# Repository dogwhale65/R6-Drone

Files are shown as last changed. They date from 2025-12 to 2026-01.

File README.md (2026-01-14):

# R6 Surveillance Drone

An open-source recreation of the surveillance drone from Rainbow Six Siege.




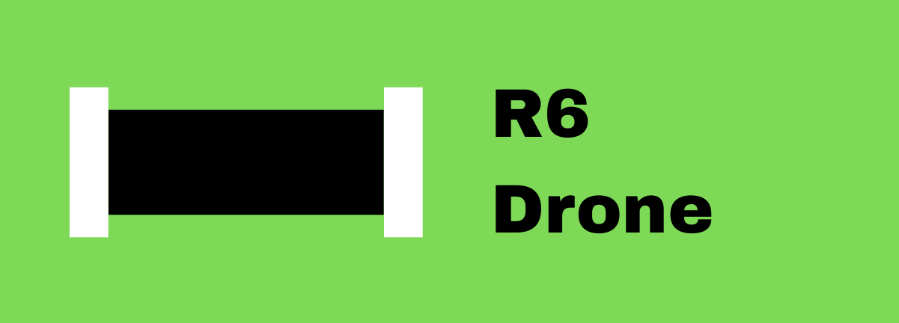
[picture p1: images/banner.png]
R6 Drone Banner


## About

I'm building a functional, 3D-printable version of the drone from R6 Siege. It features motorized wheels, LEDs, and a camera for FPV control.

Still early days — I've got the motors picked out and a rough CAD design, but there's plenty left to figure out.

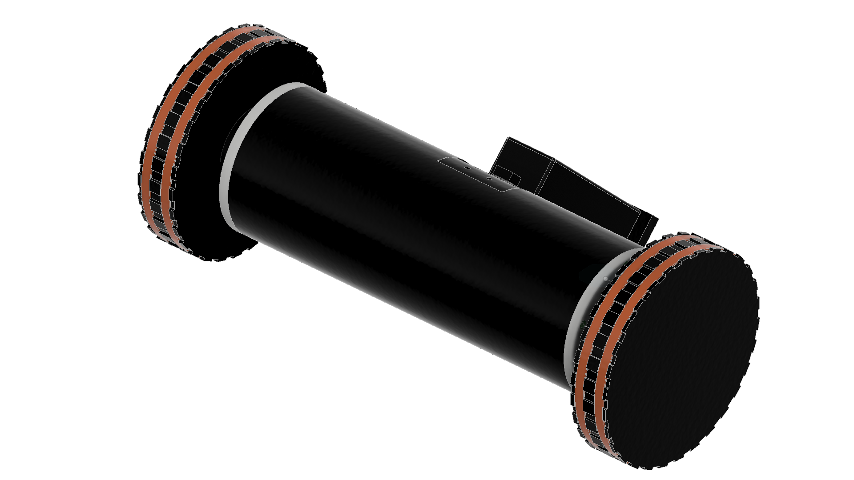
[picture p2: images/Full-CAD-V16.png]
Full CAD Design


The drone was designed to fit on a BambuLab P1S, so it may not be perfectly accurate to the in-game model. If anyone has the correct dimensions and wants to share them, I'm all ears!

I'm also *not* an engineer, so apologies if things don't work out perfectly. This is my first real project, and I'm learning as I go.

## Future Plans

- Dedicated controller
- Camera integration
- Battery level indicator

## Parts List

### Electronics

| Component | Model | Link | Qty |
| --- | ----- | ---- | --- |
| Battery | 11.1V 3S LiPo 2200mAh | [Amazon](https://www.amazon.com/dp/B07MQT6YJN) | 1 |
| Motors | 12V 550RPM | [Amazon](https://www.amazon.com/dp/B072R5G5GR) | 2 |
| Motor Driver | L298N H-Bridge | [Amazon](https://www.amazon.com/WWZMDiB-L298N-H-Bridge-Controller-Raspberry/dp/B0CR6BX5QL) | 1 |
| MCU | ESP32-S3 Dev Board | [Amazon](https://www.amazon.com/dp/B0C9GLDCRC?th=1) | 1 |
| Buck Converter | LM2596 DC-DC | [Amazon](https://www.amazon.com/dp/B08NV3JCBC) | 1 |
| XT60 Connectors | Male/Female pairs | [Amazon](https://www.amazon.com/dp/B0DB1LBGSH) | 1 pack |
| Power Switch | Rocker switch 10A, 20mm | [Amazon](https://www.amazon.com/dp/B07QQ22DTB) | 1 |
| Blue LEDs | 3mm diffused, 12V pre-wired | [Amazon](https://www.amazon.com/dp/B07T8FN8CS) | 1 pack |
| Wire | 18AWG silicone, multi-color | [Amazon](https://www.amazon.com/dp/B08BR454BX?th=1) | 1 pack |
| Heat Shrink | Assorted tubing kit | [Amazon](https://www.amazon.com/dp/B084GDLSCK) | 1 pack |
| LiPo Charger | 3S Charger | [Amazon](https://www.amazon.com/dp/B0B5GRRY59) | 1 |
| Camera | Generic Camera Module | [Amazon](https://www.amazon.com/dp/B012UXNDOY) | 1 |
| Wire Connectors | Lever nuts | [Amazon](https://www.amazon.com/dp/B0CJ5QF3VX) | 1 pack |

> **Heads up:** The motors I picked have a design flaw. Some mount holes go straight into the gearbox, so screws can hit the internals and prevent the motor from spinning. 

### 3D Printed Parts

Individual 3MF files are in `/3mf`. There's also a ready-to-print 3MF in the root folder with all parts pre-positioned and print settings configured.

> **Note:** These parts haven't been fully tested yet. They work for the most part, updates will be made as I test/improve them.

| Part | Qty | Notes |
| ---- | --- | ----- |
| Main Body | 1 | PLA or PETG, 20% infill, 3 walls, supports recommended |
| Battery Sled | 1 | PLA or PETG, 50% infill, 10 walls, support recommended |
| Motor Plates | 2 | PLA or PETG 20% infill, 5 walls |
| Wheels | 2 | TPU or PETG, 20% infill, 2 walls |

> It takes about 9 hours to print the main body and uses almost 400g of filament. I'm trying to incorporate as many features as possible into a single print to minimize this.

>The wheels are still being tested. TPU and PETG slip a lot. I'm currently working on a new design for the wheels, but cant print them at the current moment. I found out that if you just put some rubber bands around the wheels, it works just fine, but they fall off if you take a turn too hard. New wheel design will be posted soon, which has grooves for the rubber bands to stay in place better.

### Wheel Design Iterations

1. Just a simple cutout for the shaft. It stripped the wheels and obviously fell off.
2. Same principle but I added a screw hole to screw in and clamp onto the D-shaft. Worked good at preventing stripping, but still fell off.
3. A clamp system that used 2 screws to clamp around the shaft. Worked just about the same as the original wheel. The screws stripped the plastic before any real torque could be applied to it to actually clamp.
4. Current design, a separate hub that screws both onto/into the D-shaft and the wheel respectively. Haven't printed it yet, but I think it will work.

Print at 0.2mm layer height with supports where needed.

## Wiring

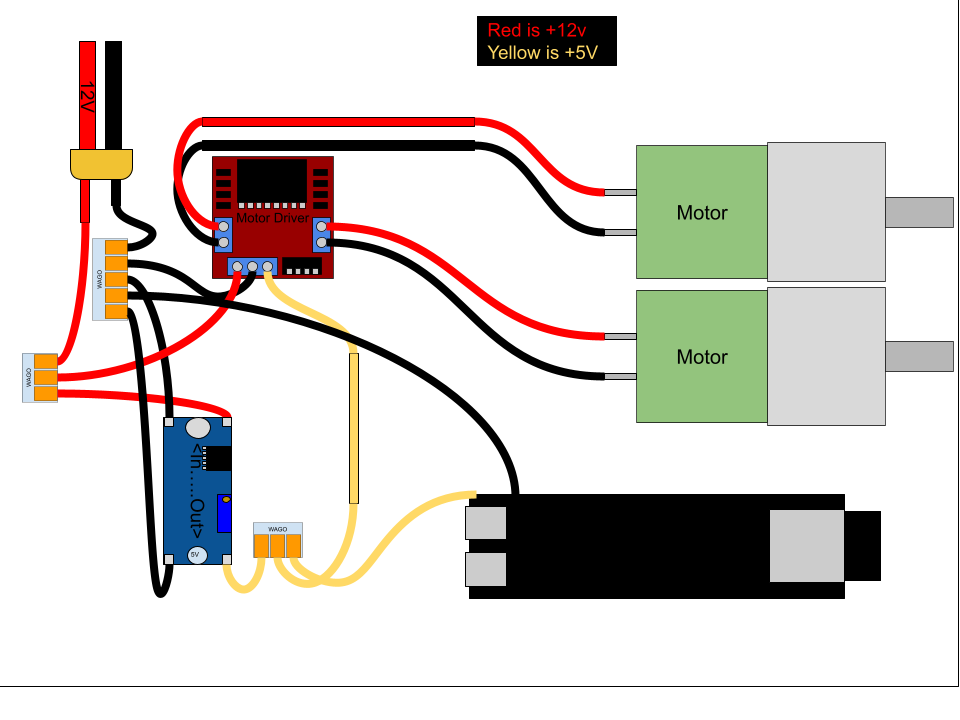
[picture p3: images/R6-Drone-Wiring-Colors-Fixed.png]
Wiring Diagram


**Notes:**

- This diagram doesn't include switches or extras.
- Logic wires aren't shown yet — I'll add them in a future revision.
- In my first build, I messed up my ESP32 and broke the 5V connection on my ESP32. I worked around it by adding a second buck converter and powering via the 3.3V pin instead.

Logic wires:

- ENA → GPIO 5
- IN1 → GPIO 6
- IN2 → GPIO 7
- ENB → GPIO 8
- IN3 → GPIO 9
- IN4 → GPIO 10

## Assembly

> **Note:** I used M3 x 20mm screws because I had them lying around. Shorter screws work for the motor plates, but I'd recommend at least 20mm for the main body.

1. Attach the motor plates to the motors, ensuring the motors can still spin freely.
2. Mount the motor plates to the bottom half of the main body.
3. Install the electronics inside the main body.
4. Attach the top half of the main body to the motor plates.
5. Secure the two body halves together.

## Code

The code is in `/code`. It runs a simple web server for controlling the drone. Connect to the drone's WiFi, open the web interface, and drive using on-screen joystick controls or WASD keys on a keyboard. Connect to it by connecting to the drone's WiFi network and visiting `http://192.168.4.1` in your browser. The default password is `password123` on the network `Robot-ESP32`

I am working on making an actual controller for it, rather than using my phone or a computer. Currently, there's a Bluetooth version for mobile app control.

## License

MIT — see [LICENSE](LICENSE).

---

[github.com/dogwhale65/r6-drone](https://github.com/dogwhale65/r6-drone)

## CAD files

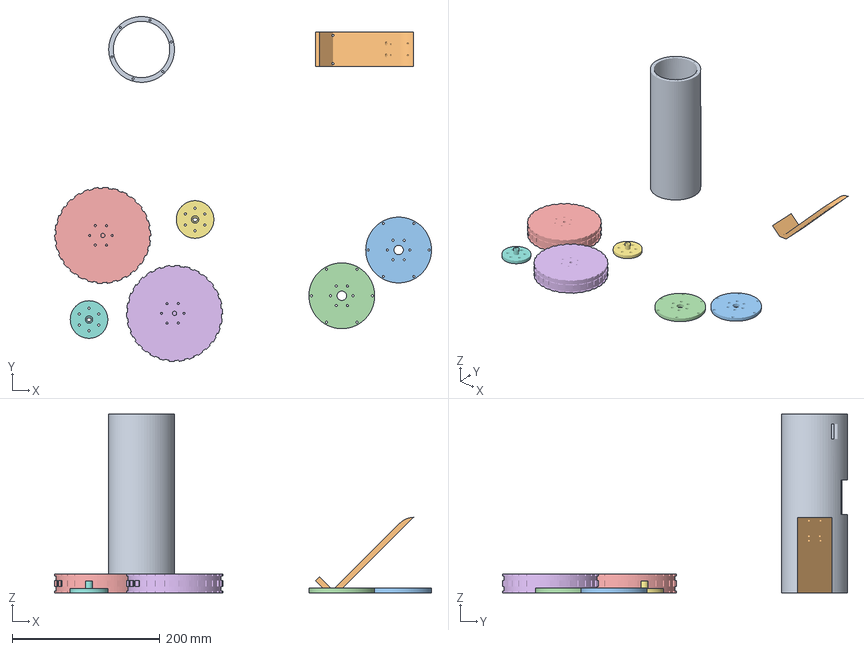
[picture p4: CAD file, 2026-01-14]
3mf/Full-Drone-BS.3mf
509.6 x 466.1 x 241.3 mm
Sled
Motor Plate x 2
Wheel (1) x 2

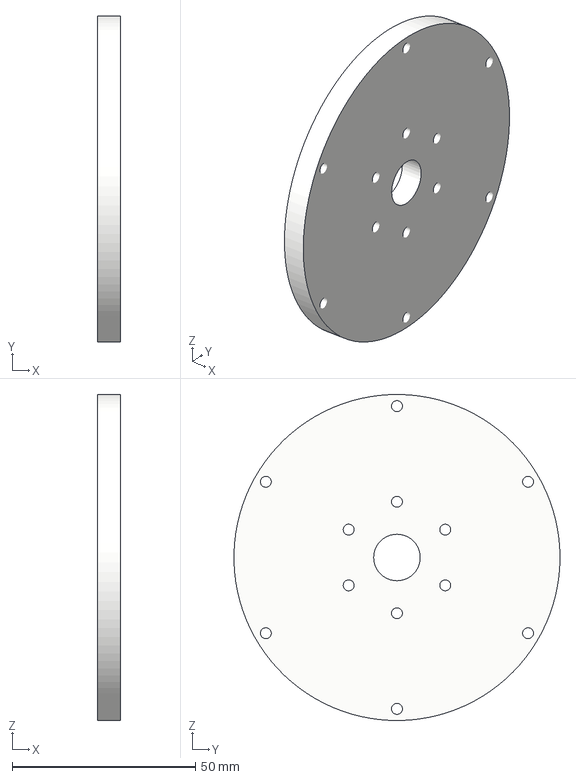
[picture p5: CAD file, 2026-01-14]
3mf/Motor-Plate.3mf
6.35 x 88.9 x 88.9 mm

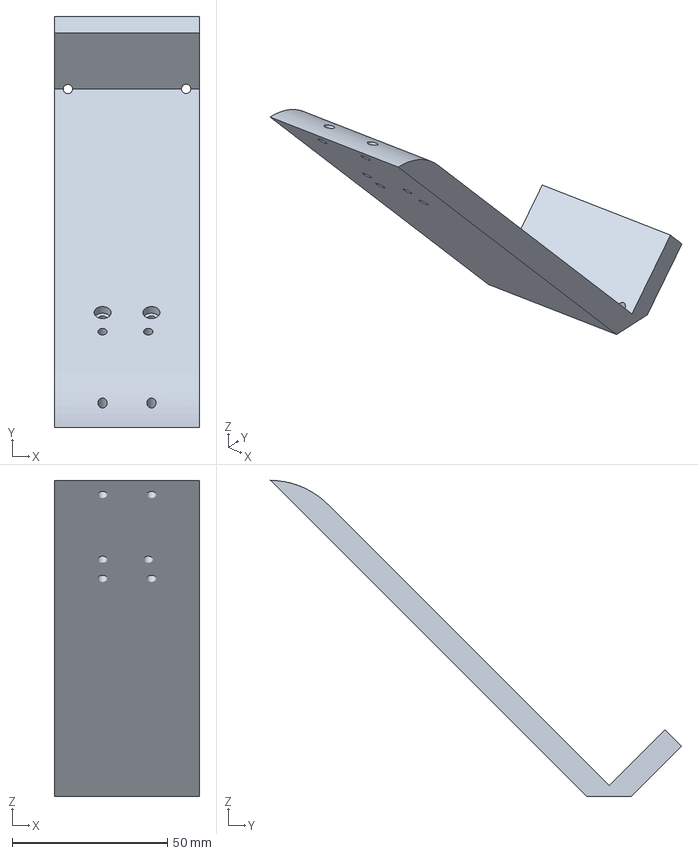
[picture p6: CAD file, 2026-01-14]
3mf/Battery-Sled.3mf
46.7 x 132.5 x 102.0 mm

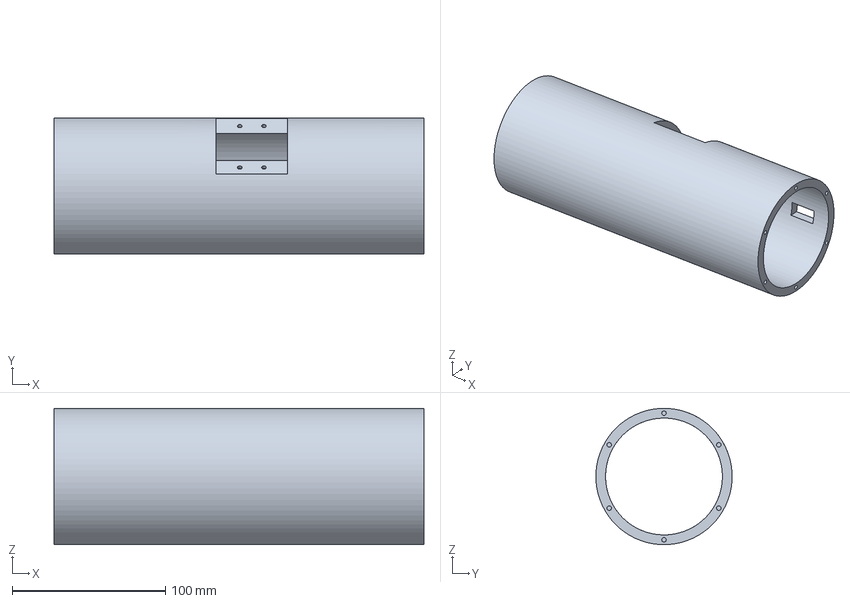
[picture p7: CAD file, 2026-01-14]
3mf/Body.3mf
241.3 x 88.9 x 88.9 mm

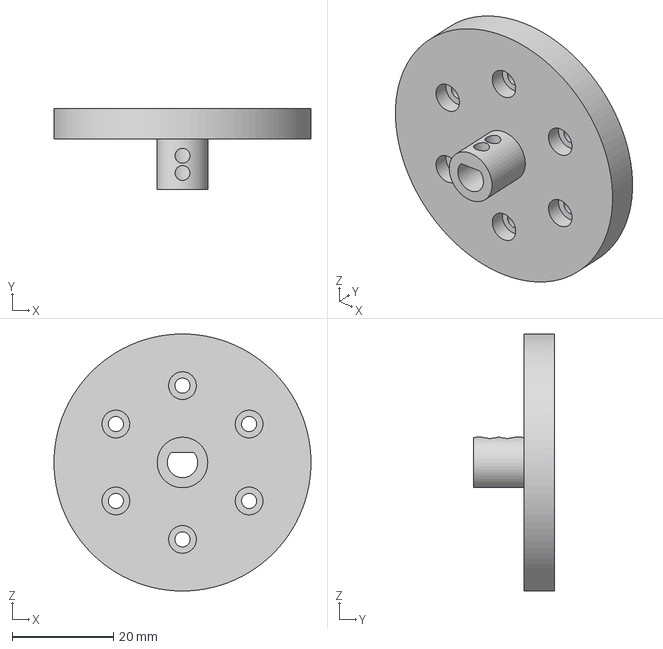
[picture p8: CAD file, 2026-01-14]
3mf/Wheel-Hub.3mf
50.8 x 16.0 x 50.8 mm

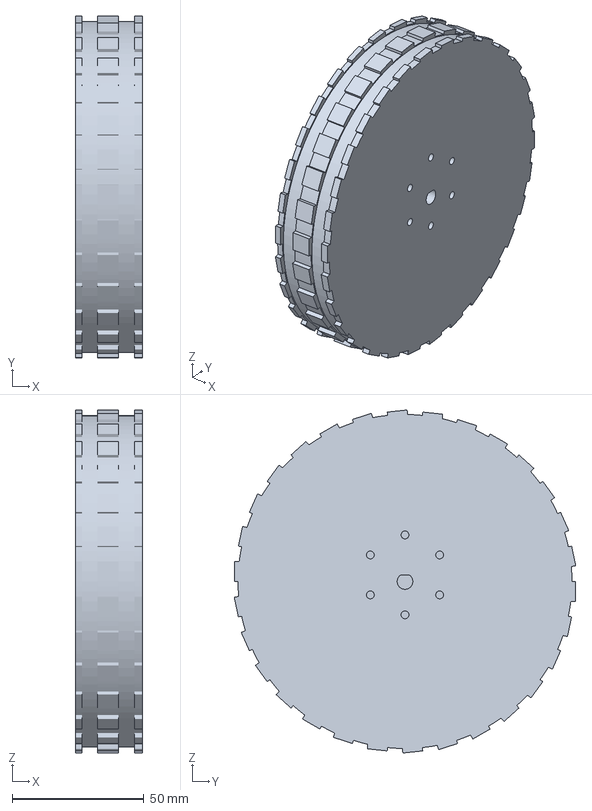
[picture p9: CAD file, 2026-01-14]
3mf/Wheel.3mf
25.4 x 129.9 x 130.4 mm

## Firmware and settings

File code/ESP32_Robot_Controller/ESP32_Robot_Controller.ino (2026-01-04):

#include <WiFi.h>
#include <WebServer.h>
#include <Adafruit_NeoPixel.h>

const char* ssid = "Robot-ESP32";
const char* password = "password123";

const int ENA = 5;
const int IN1 = 6;
const int IN2 = 7;
const int ENB = 8;
const int IN3 = 9;
const int IN4 = 10;

#define RGB_PIN 48
#define NUM_PIXELS 1
Adafruit_NeoPixel pixels(NUM_PIXELS, RGB_PIN, NEO_GRB + NEO_KHZ800);

const int pwmFreq = 20000;
const int pwmResolution = 8;

WebServer server(80);

int throttle = 0;
int rotation = 0;

void setLED(int r, int g, int b) {
  pixels.setPixelColor(0, pixels.Color(r, g, b));
  pixels.show();
}

void updateLED() {
  int r = 0, g = 0, b = 0;
  
  if (throttle > 10) { 
    r = 255; g = 255; b = 255; 
  } else if (throttle < -10) { 
    r = 255; g = 0; b = 0; 
  }
  
  if (rotation < -10) {
    if (throttle > 10) { 
      r = 0; g = 255; b = 255;
    } else if (throttle < -10) { 
      r = 255; g = 255; b = 0;
    } else { 
      r = 0; g = 255; b = 0;
    }
  } else if (rotation > 10) {
    if (throttle > 10) { 
      r = 128; g = 128; b = 255;
    } else if (throttle < -10) { 
      r = 255; g = 0; b = 255;
    } else { 
      r = 0; g = 0; b = 255;
    }
  }
  
  setLED(r, g, b);
}

void setMotor(int pwmPin, int inA, int inB, int speed) {
  speed = constrain(speed, -100, 100);
  
  if (speed > 0) {
    digitalWrite(inA, HIGH);
    digitalWrite(inB, LOW);
  } else if (speed < 0) {
    digitalWrite(inA, LOW);
    digitalWrite(inB, HIGH);
  } else {
    digitalWrite(inA, LOW);
    digitalWrite(inB, LOW);
  }
  
  int pwm = map(abs(speed), 0, 100, 0, 255);
  ledcWrite(pwmPin, pwm);
}

void updateMotors() {
  int left = constrain(throttle - rotation, -100, 100);
  int right = constrain(throttle + rotation, -100, 100);
  
  setMotor(ENA, IN1, IN2, left);
  setMotor(ENB, IN3, IN4, right);
  updateLED();
}

void handleControl() {
  if (server.hasArg("t")) throttle = server.arg("t").toInt();
  if (server.hasArg("r")) rotation = server.arg("r").toInt();
  
  updateMotors();
  server.send(200, "text/plain", "OK");
}

void handleRoot() {
  server.send(200, "text/html", R"rawliteral(
<!DOCTYPE html>
<html lang="en">
<head>
<meta name="viewport" content="width=device-width, initial-scale=1">
<style>
:root {
  --bg: #0e0f12;
  --panel: #151821;
  --border: #2a2f3a;
  --text: #e6e6e6;
  --muted: #9aa0aa;
  --accent: #4da3ff;
}

* {
  box-sizing: border-box;
}

body {
  margin: 0;
  font-family: system-ui, -apple-system, Segoe UI, Roboto, sans-serif;
  background: var(--bg);
  color: var(--text);
  min-height: 100vh;
  display: flex;
  align-items: center;
  justify-content: center;
}

.container {
  width: 100%;
  max-width: 900px;
  padding: 24px;
}

header {
  margin-bottom: 32px;
  text-align: center;
}

header h1 {
  margin: 0;
  font-size: 26px;
  font-weight: 500;
}

header p {
  margin-top: 6px;
  font-size: 14px;
  color: var(--muted);
}

.controls {
  display: flex;
  gap: 48px;
  justify-content: center;
  flex-wrap: wrap;
}

.control-group {
  background: var(--panel);
  border: 1px solid var(--border);
  border-radius: 12px;
  padding: 20px 24px 24px;
  text-align: center;
}

.control-group h2 {
  margin: 0 0 14px;
  font-size: 14px;
  font-weight: 500;
  color: var(--muted);
  letter-spacing: 0.5px;
}

.joy {
  width: 200px;
  height: 200px;
  border-radius: 50%;
  background: #0b0d13;
  border: 2px solid var(--border);
  position: relative;
  touch-action: none;
}

.knob {
  width: 64px;
  height: 64px;
  border-radius: 50%;
  background: var(--accent);
  position: absolute;
  left: 68px;
  top: 68px;
  box-shadow: 0 6px 16px rgba(0,0,0,0.5);
}

.info {
  margin-top: 32px;
  display: grid;
  grid-template-columns: 1fr 1fr;
  gap: 20px;
}

.card {
  background: var(--panel);
  border: 1px solid var(--border);
  border-radius: 12px;
  padding: 16px 18px;
  font-size: 14px;
}

.card h3 {
  margin: 0 0 10px;
  font-size: 14px;
  font-weight: 500;
  color: var(--muted);
}

.key-list span {
  display: inline-block;
  padding: 2px 6px;
  margin: 0 4px;
  border: 1px solid var(--border);
  border-radius: 4px;
  font-size: 12px;
  background: #0b0d13;
}

.color-grid {
  display: grid;
  grid-template-columns: repeat(auto-fit, minmax(140px, 1fr));
  gap: 8px;
}

.color-item {
  display: flex;
  align-items: center;
  gap: 8px;
}

.color-box {
  width: 12px;
  height: 12px;
  border-radius: 3px;
}

@media (max-width: 600px) {
  .controls {
    gap: 24px;
  }
  .joy {
    width: 170px;
    height: 170px;
  }
  .knob {
    width: 54px;
    height: 54px;
    left: 58px;
    top: 58px;
  }
  .info {
    grid-template-columns: 1fr;
  }
}
</style>
</head>
<body>

<div class="container">

  <header>
    <h1>Robot Control</h1>
    <p>Web-based manual drive interface</p>
  </header>

  <div class="controls">
    <div class="control-group">
      <h2>Throttle</h2>
      <div class="joy" id="throttle">
        <div class="knob"></div>
      </div>
    </div>

    <div class="control-group">
      <h2>Rotation</h2>
      <div class="joy" id="rotate">
        <div class="knob"></div>
      </div>
    </div>
  </div>

  <div class="info">
    <div class="card">
      <h3>Keyboard control</h3>
      <div class="key-list">
        <span>W</span><span>S</span> throttle
        &nbsp;&nbsp;
        <span>A</span><span>D</span> rotation
      </div>
    </div>

    <div class="card">
      <h3>LED status</h3>
      <div class="color-grid">
        <div class="color-item"><span class="color-box" style="background:white"></span>Forward</div>
        <div class="color-item"><span class="color-box" style="background:red"></span>Backward</div>
        <div class="color-item"><span class="color-box" style="background:lime"></span>Left</div>
        <div class="color-item"><span class="color-box" style="background:blue"></span>Right</div>
        <div class="color-item"><span class="color-box" style="background:cyan"></span>Forward + Left</div>
        <div class="color-item"><span class="color-box" style="background:lightblue"></span>Forward + Right</div>
        <div class="color-item"><span class="color-box" style="background:yellow"></span>Back + Left</div>
        <div class="color-item"><span class="color-box" style="background:magenta"></span>Back + Right</div>
      </div>
    </div>
  </div>

</div>

<script>
function joystick(el, callback) {
  const knob = el.querySelector('.knob');
  const center = el.offsetWidth / 2;
  const limit = center - knob.offsetWidth / 2;

  function move(x, y) {
    const dx = x - center;
    const dy = y - center;
    const dist = Math.min(limit, Math.hypot(dx, dy));
    const angle = Math.atan2(dy, dx);
    const nx = Math.cos(angle) * dist;
    const ny = Math.sin(angle) * dist;
    knob.style.left = center + nx - knob.offsetWidth / 2 + "px";
    knob.style.top = center + ny - knob.offsetHeight / 2 + "px";
    callback(nx / limit, -ny / limit);
  }

  el.addEventListener("touchmove", e => {
    const t = e.touches[0];
    const r = el.getBoundingClientRect();
    move(t.clientX - r.left, t.clientY - r.top);
    e.preventDefault();
  });

  el.addEventListener("touchend", () => {
    knob.style.left = (center - knob.offsetWidth / 2) + "px";
    knob.style.top = (center - knob.offsetHeight / 2) + "px";
    callback(0, 0);
  });
}

let throttle = 0;
let rotation = 0;
let keysPressed = {};

function send() {
  fetch(`/control?t=${Math.round(throttle*100)}&r=${Math.round(rotation*100)}`);
}

function updateFromKeys() {
  let t = 0, r = 0;
  if (keysPressed.w) t++;
  if (keysPressed.s) t--;
  if (keysPressed.a) r--;
  if (keysPressed.d) r++;
  throttle = t;
  rotation = r;
  send();
}

document.addEventListener('keydown', e => {
  const k = e.key.toLowerCase();
  if ("wasd".includes(k)) {
    e.preventDefault();
    keysPressed[k] = true;
    updateFromKeys();
  }
});

document.addEventListener('keyup', e => {
  const k = e.key.toLowerCase();
  if ("wasd".includes(k)) {
    e.preventDefault();
    delete keysPressed[k];
    updateFromKeys();
  }
});

joystick(document.getElementById("throttle"), (x, y) => {
  if (!Object.keys(keysPressed).length) {
    throttle = y;
    send();
  }
});

joystick(document.getElementById("rotate"), (x) => {
  if (!Object.keys(keysPressed).length) {
    rotation = x;
    send();
  }
});
</script>

</body>
</html>
)rawliteral");
}


void setup() {
  Serial.begin(115200);
  
  pinMode(IN1, OUTPUT);
  pinMode(IN2, OUTPUT);
  pinMode(IN3, OUTPUT);
  pinMode(IN4, OUTPUT);

  ledcAttach(ENA, pwmFreq, pwmResolution);
  ledcAttach(ENB, pwmFreq, pwmResolution);

  pixels.begin();
  pixels.setBrightness(50);
  setLED(0, 0, 0);

  WiFi.softAP(ssid, password);
  
  Serial.println("WiFi AP Started");
  Serial.print("IP Address: ");
  Serial.println(WiFi.softAPIP());

  server.on("/", handleRoot);
  server.on("/control", handleControl);
  server.begin();
  
  Serial.println("Server started");
}

void loop() {
  server.handleClient();
}

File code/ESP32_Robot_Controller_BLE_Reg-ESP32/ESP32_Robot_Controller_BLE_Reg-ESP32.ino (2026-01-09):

#include <BLEDevice.h>
#include <BLEServer.h>
#include <BLEUtils.h>
#include <BLE2902.h>
#include <Adafruit_NeoPixel.h>

// BLE UUIDs - These must match in the Android app
#define SERVICE_UUID        "4fafc201-1fb5-459e-8fcc-c5c9c331914b"
#define THROTTLE_CHAR_UUID  "beb5483e-36e1-4688-b7f5-ea07361b26a8"
#define ROTATION_CHAR_UUID  "1c95d5e3-d8f7-413a-bf3d-7a2e5d7be87e"

// Motor pins - adjusted for WROOM-32
const int ENA = 25;  // PWM capable pins
const int IN1 = 26;
const int IN2 = 27;
const int ENB = 32;
const int IN3 = 33;
const int IN4 = 14;

// RGB LED - changed to a valid WROOM-32 pin
#define RGB_PIN 13  // GPIO13 is available on WROOM-32
#define NUM_PIXELS 1
Adafruit_NeoPixel pixels(NUM_PIXELS, RGB_PIN, NEO_GRB + NEO_KHZ800);

// PWM settings
const int pwmFreq = 20000;
const int pwmResolution = 8;

// BLE objects
BLEServer *pServer = NULL;
BLECharacteristic *throttleCharacteristic = NULL;
BLECharacteristic *rotationCharacteristic = NULL;
bool deviceConnected = false;

// Control values
int throttle = 0;
int rotation = 0;

// Watchdog timer for lost commands
unsigned long lastCommandTime = 0;
const unsigned long COMMAND_TIMEOUT = 500; // 500ms timeout

void setLED(int r, int g, int b) {
  pixels.setPixelColor(0, pixels.Color(r, g, b));
  pixels.show();
}

void updateLED() {
  int r = 0, g = 0, b = 0;
  
  // Forward/backward status
  if (throttle > 10) { 
    r = 255; g = 255; b = 255; // White - forward
  } else if (throttle < -10) { 
    r = 255; g = 0; b = 0; // Red - backward
  }
  
  // Rotation status overlays
  if (rotation < -10) { // Left turn
    if (throttle > 10) { 
      r = 0; g = 255; b = 255; // Cyan - forward + left
    } else if (throttle < -10) { 
      r = 255; g = 255; b = 0; // Yellow - backward + left
    } else { 
      r = 0; g = 255; b = 0; // Green - left only
    }
  } else if (rotation > 10) { // Right turn
    if (throttle > 10) { 
      r = 128; g = 128; b = 255; // Light blue - forward + right
    } else if (throttle < -10) { 
      r = 255; g = 0; b = 255; // Magenta - backward + right
    } else { 
      r = 0; g = 0; b = 255; // Blue - right only
    }
  }
  
  setLED(r, g, b);
}

void setMotor(int pwmPin, int inA, int inB, int speed) {
  speed = constrain(speed, -100, 100);
  
  if (speed > 0) {
    digitalWrite(inA, HIGH);
    digitalWrite(inB, LOW);
  } else if (speed < 0) {
    digitalWrite(inA, LOW);
    digitalWrite(inB, HIGH);
  } else {
    digitalWrite(inA, LOW);
    digitalWrite(inB, LOW);
  }
  
  int pwm = map(abs(speed), 0, 100, 0, 255);
  ledcWrite(pwmPin, pwm);
}

void updateMotors() {
  // Tank drive: left = throttle - rotation, right = throttle + rotation
  int left = constrain(throttle - rotation, -100, 100);
  int right = constrain(throttle + rotation, -100, 100);
  
  setMotor(ENA, IN1, IN2, left);
  setMotor(ENB, IN3, IN4, right);
  updateLED();
}

void checkCommandTimeout() {
  // If no command received in COMMAND_TIMEOUT ms, stop the robot
  if (deviceConnected && (millis() - lastCommandTime > COMMAND_TIMEOUT)) {
    if (throttle != 0 || rotation != 0) {
      throttle = 0;
      rotation = 0;
      updateMotors();
      Serial.println("Command timeout - stopping motors");
    }
  }
}

// Server callbacks for connection status
class ServerCallbacks: public BLEServerCallbacks {
    void onConnect(BLEServer* pServer) {
      deviceConnected = true;
      Serial.println("Device connected");
      setLED(0, 255, 0); // Green when connected
      delay(500);
      updateLED(); // Return to status LED
    }

    void onDisconnect(BLEServer* pServer) {
      deviceConnected = false;
      Serial.println("Device disconnected");
      throttle = 0;
      rotation = 0;
      updateMotors();
      setLED(255, 0, 0); // Red when disconnected
      
      // Restart advertising
      BLEDevice::startAdvertising();
      Serial.println("Waiting for connection...");
    }
};

// Characteristic callbacks for receiving control values
class ControlCallbacks: public BLECharacteristicCallbacks {
    void onWrite(BLECharacteristic *pCharacteristic) {
        String value = pCharacteristic->getValue().c_str();
        
        if (value.length() > 0) {
            int val = value.toInt();
            val = constrain(val, -100, 100); // Safety constraint
            
            if (pCharacteristic->getUUID().toString() == THROTTLE_CHAR_UUID) {
                throttle = val;
                Serial.print("Throttle: ");
                Serial.println(throttle);
            } else if (pCharacteristic->getUUID().toString() == ROTATION_CHAR_UUID) {
                rotation = val;
                Serial.print("Rotation: ");
                Serial.println(rotation);
            }
            
            lastCommandTime = millis(); // Update watchdog timer
            updateMotors();
        }
    }
};

void setup() {
  Serial.begin(115200);
  Serial.println("Starting BLE Robot Control...");
  
  // Configure motor pins
  pinMode(IN1, OUTPUT);
  pinMode(IN2, OUTPUT);
  pinMode(IN3, OUTPUT);
  pinMode(IN4, OUTPUT);

  // Setup PWM using new API (works on both S3 and WROOM-32 with newer core)
  ledcAttach(ENA, pwmFreq, pwmResolution);
  ledcAttach(ENB, pwmFreq, pwmResolution);

  // Initialize RGB LED
  pixels.begin();
  pixels.setBrightness(50);
  setLED(255, 0, 0); // Red on startup

  // Initialize BLE
  BLEDevice::init("Robot-ESP32");
  
  // Create BLE Server
  pServer = BLEDevice::createServer();
  pServer->setCallbacks(new ServerCallbacks());

  // Create BLE Service
  BLEService *pService = pServer->createService(SERVICE_UUID);

  // Create Throttle Characteristic
  throttleCharacteristic = pService->createCharacteristic(
                              THROTTLE_CHAR_UUID,
                              BLECharacteristic::PROPERTY_READ |
                              BLECharacteristic::PROPERTY_WRITE
                            );
  throttleCharacteristic->setCallbacks(new ControlCallbacks());
  throttleCharacteristic->setValue("0");

  // Create Rotation Characteristic
  rotationCharacteristic = pService->createCharacteristic(
                              ROTATION_CHAR_UUID,
                              BLECharacteristic::PROPERTY_READ |
                              BLECharacteristic::PROPERTY_WRITE
                            );
  rotationCharacteristic->setCallbacks(new ControlCallbacks());
  rotationCharacteristic->setValue("0");

  // Start the service
  pService->start();

  // Start advertising
  BLEAdvertising *pAdvertising = BLEDevice::getAdvertising();
  pAdvertising->addServiceUUID(SERVICE_UUID);
  pAdvertising->setScanResponse(true);
  pAdvertising->setMinPreferred(0x06);
  pAdvertising->setMinPreferred(0x12);
  BLEDevice::startAdvertising();
  
  Serial.println("BLE Robot ready!");
  Serial.println("Waiting for connection...");
  setLED(0, 0, 255); // Blue when waiting
  
  lastCommandTime = millis(); // Initialize watchdog
}

void loop() {
  checkCommandTimeout(); // Safety feature
  delay(10);
}

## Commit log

2025-12-23 Refactor parts list in README to consolidate motor information
2025-12-23 added Wiring diagram
2025-12-23 added 3mf files
    [R6-Drone_Full-Print-Bambu.3mf, R6-Drone_Main-Body-Bottom.3mf, R6-Drone_Main-Body-Top.3mf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]
2025-12-23 Update LiPo Charger description in README
2025-12-23 Update camera module description in README
2025-12-23 Fix Camera link in README.md
2026-01-04 Finalized model as well as other changes
    [Battery-Sled.3mf, Main-Body.3mf, Motor-Plate.3mf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]
2026-01-14 Update README with future plans, parts list adjustments, and wheel design iterations
2026-01-14 Updated CAD Files
    [Battery-Sled.3mf, Body.3mf, Full-Drone-BS.3mf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]
2026-01-14 Added CAD image
